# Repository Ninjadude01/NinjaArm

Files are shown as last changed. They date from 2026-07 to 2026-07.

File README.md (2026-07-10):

## NinjaArm
NinjaArm is a custom robotic arm with 3 degrees of freedom + a claw. It uses an Arduino Uno along with a servo board, 3 servos, 1 micro servo, and 4 potentiometers to control rotation. It includes a small stand for the potentiometers, and a larger display stand to hold the servo board and Arduino. I decided to create a robotic arm beacuse after building a working keyboard in real life I wanted a larger and more ambitious project. I thought that robotic arms seemed cool, so I decided to create my own from scratch. 

## Renders
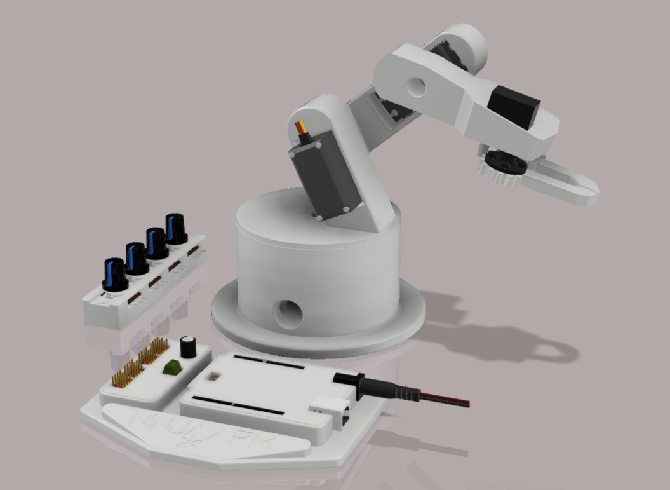
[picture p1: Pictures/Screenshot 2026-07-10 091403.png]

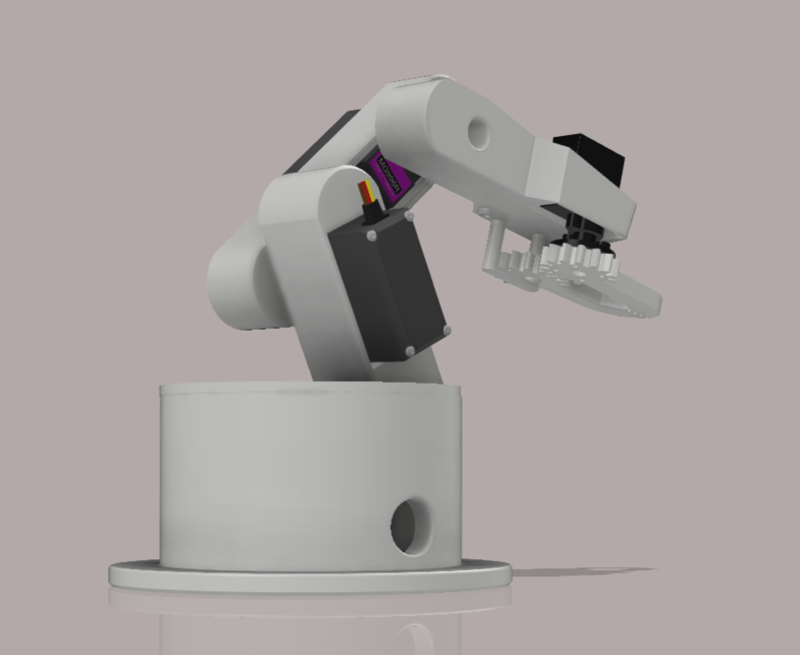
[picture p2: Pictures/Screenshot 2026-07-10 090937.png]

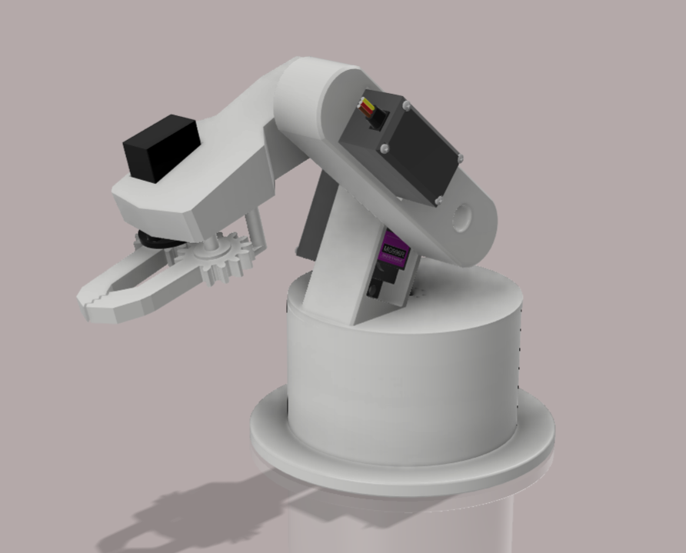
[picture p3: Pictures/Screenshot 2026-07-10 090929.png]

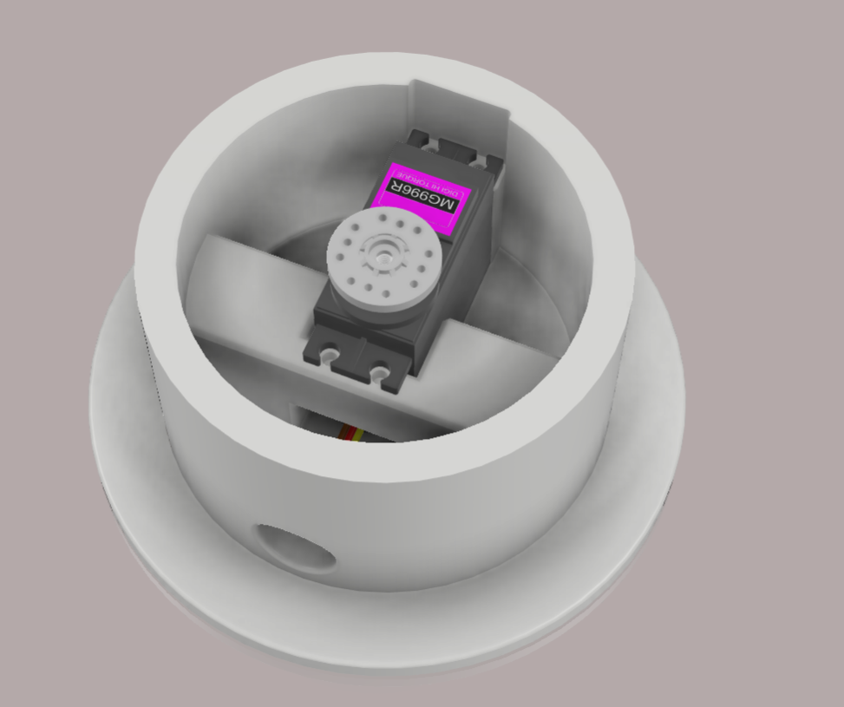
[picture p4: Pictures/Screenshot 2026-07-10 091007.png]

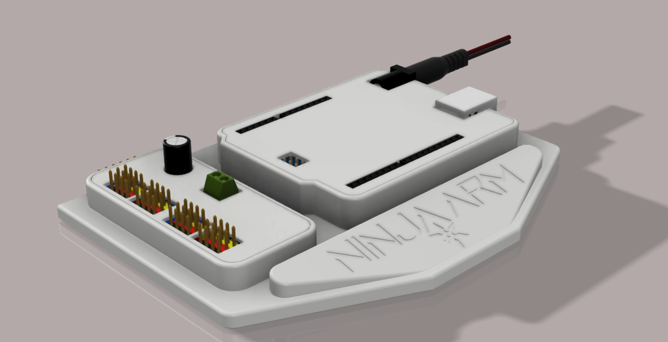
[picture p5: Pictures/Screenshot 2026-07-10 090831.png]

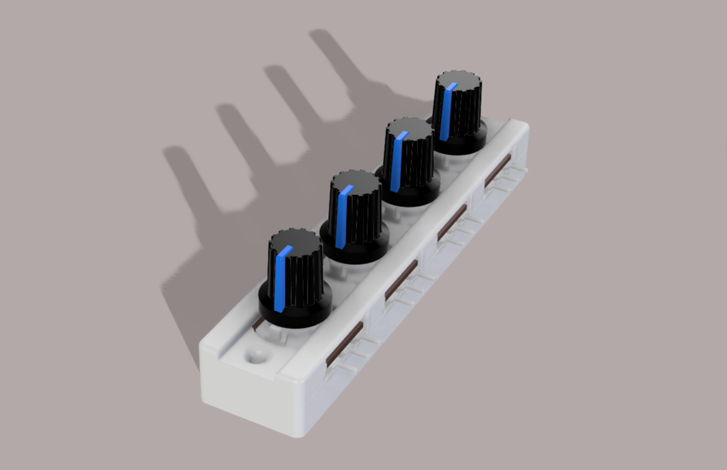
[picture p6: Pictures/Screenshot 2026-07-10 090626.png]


## Schematic Diagram
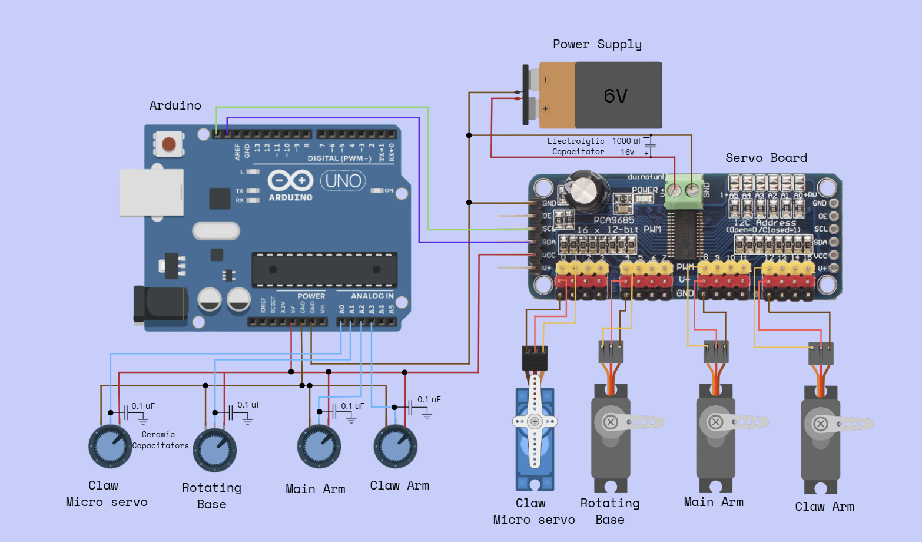
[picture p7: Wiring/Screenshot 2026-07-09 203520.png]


## Steps to Reproduce
1. Purchase all materials listed in the BOM, and print all needed parts from the CAD folder.
2. Align the heatset inserts in the correct locations and use a soldering iron set to 200℃ to slowly push them into place.
3. Place the 4 potentiometers into the knob case, put the lid ontop, and screw it into place. You can now place the knob covers ontop.
4. Place the arduino and servo board onto their respective spots on the display stand, and cover them with the lids.
5. Insert a servo into the base, main arm, and claw arm, and use the 6mm m2 screw to secure them. Insert the micro servo into the claw arm and screw that in as well.
6. Connect the micro servo horn to a claw using screws, align the second claw in the correct location, and quickly place the claw connector beneath it (screw this in as well).
7. Grab a servo horns and use 4 metal self tapping screws to secure it to its corresponding robo arm part. Repeat this two more times.
8. Use the servo horn screws to connect all three horns to their servos.
9. Follow the wiring diagram and connect all wires to the correct spots.
10. Download the .ino file found in the firmware folder, and flash it onto your arduino.
11. Use the potentiometers to control the arms, and enjoy playing with your very own NinjaArm!

Note: AI was used to assist with the firmware of this project.
## BOM
|Item|Part Name |Quantity|Description |Cost (USD)|Link |
|----|---|---|---|---|---|
|1 |Arduino Uno |1 |Microcontroller |$6.82 |https://www.aliexpress.com/item/1005012021584902.html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 |
|2 |Servo Motors |3 |MG996R (metal 180) |$13.47 |https://www.aliexpress.com/item/1005006525247038.html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 |
|3 |Smaller Servo |1 |MG90S (metal 180) |$4.42 |https://www.aliexpress.com/item/1005008626768357.html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 |
|4 |Servo Driver Board |1 | PCA9685 |$3.77 |https://www.aliexpress.com/item/1005008717177681.html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 |
|5 |Heatset Inserts |100 |M2 |$3.55 |https://www.aliexpress.com/item/1005006838108683.html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 |
|6 |Screws |50 |M2, 6mm |$1.69 |https://www.aliexpress.com/item/32973784147.html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 |
|7 |Electrolytic Capacitators|10 |1000 uF, 16v |$1.28 |https://www.aliexpress.com/item/1005005557021801.html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 |
|8 |Ceramic Capacitators |10 |0.1 uF |$3.88 |https://www.aliexpress.com/item/1005007851933584.html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 |
|9 |Stranded wire |1 |20 AWG (5m, black +red) |$7.57 |https://www.aliexpress.com/item/1005006250522147.html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|
|10  |Stranded wire |1 |22 AWG (5m, 5pc multicolor)|$15.39 |https://www.aliexpress.com/item/1005006350734418.html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 |
|11  |Potentiometers |4 |To control rotation (B10k) |$6.52 |https://www.aliexpress.com/item/1005010063122061.html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 |
|12  |Pot Knob Cap |30 |For protection |$2.99 |https://www.aliexpress.com/item/1005008733564858.html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 |
|13  |Rubber bumpers |10 |For tip of robot arm |$3.78 |https://www.aliexpress.com/item/1005003881918836.html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 |
|14  |6v power supply |1 |10A |$27.33 |https://www.aliexpress.com/item/1005008119363339.html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 |
| | | | | | |
| | | |Total |$102.46 |

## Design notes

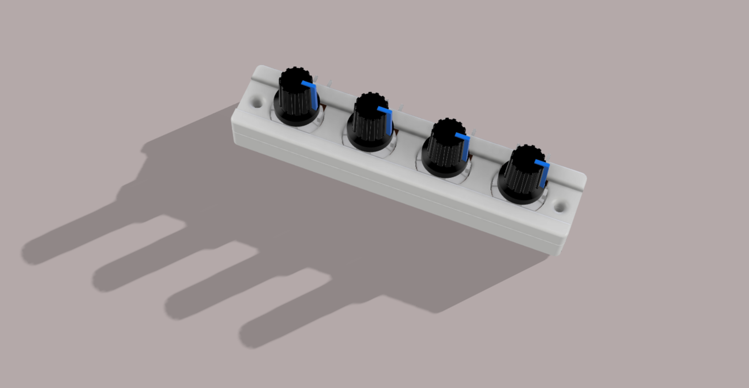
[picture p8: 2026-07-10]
Pictures/Screenshot 2026-07-10 090645.png

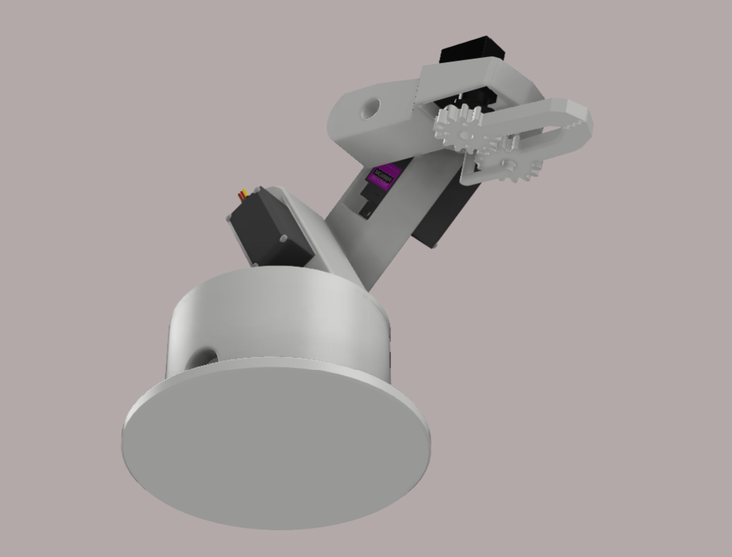
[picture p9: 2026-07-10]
Pictures/Screenshot 2026-07-10 090954.png

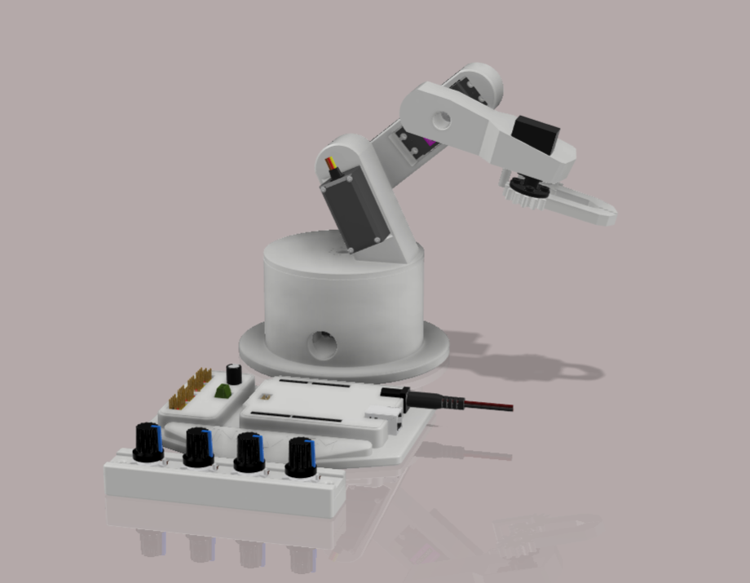
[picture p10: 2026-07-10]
Pictures/Screenshot 2026-07-10 091027.png

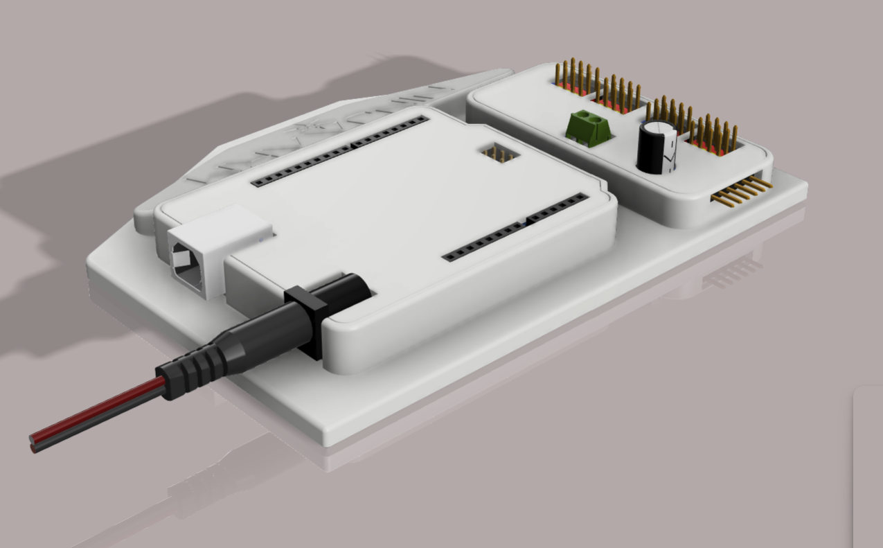
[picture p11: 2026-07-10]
Pictures/Screenshot 2026-07-10 090838.png

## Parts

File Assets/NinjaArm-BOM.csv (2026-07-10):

Item | Part Name | Quantity | Description | Cost (USD) | Link
1 | Arduino Uno | 1 | Microcontroller | $6.82 | https://www.aliexpress.com/item/1005012021584902.html?curPageLogUid=nl1zu1W5NWxa
2 | Servo Motors | 3 | MG996R (metal 180) | $13.47 | https://www.aliexpress.com/item/1005006525247038.html?mp=1
3 | Smaller Servo | 1 | MG90S (metal 180) | $4.42 | https://www.aliexpress.com/item/1005008626768357.html?mp=1
4 | Servo Driver Board | 1 | PCA9685 | $3.77 | https://www.aliexpress.com/item/1005008717177681.html?curPageLogUid=hQarf3Dfmsxr
5 | Heatset Inserts | 100 | M2 | $3.55 | https://www.aliexpress.com/item/1005006838108683.html?mp=1
6 | Screws | 50 | M2, 6mm | $1.69 | https://www.aliexpress.com/item/32973784147.html?mp=1
7 | Electrolytic Capacitators | 10 | 1000 uF, 16v | $1.28 | https://www.aliexpress.com/item/1005005557021801.html?curPageLogUid=4GRgiLxo8gIg
8 | Ceramic Capacitators | 10 | 0.1 uF | $3.88 | https://www.aliexpress.com/item/1005007851933584.html?curPageLogUid=3pynuA3Hzad2
9 | Stranded wire | 1 | 20 AWG (5m, black +red) | $7.57 | https://www.aliexpress.com/item/1005006250522147.html?curPageLogUid=9vo7UWaH5KD7
10 | Stranded wire | 1 | 22 AWG (5m, 5pc multicolor) | $15.39 | https://www.aliexpress.com/item/1005006350734418.html?curPageLogUid=8tPYifazeFcG
11 | Potentiometers | 4 | To control rotation (B10k) | $6.52 | https://www.aliexpress.com/item/1005010063122061.html?mp=1
12 | Pot Knob Cap | 30 | For protection | $2.99 | https://www.aliexpress.com/item/1005008733564858.html?curPageLogUid=KjNbnIj9rQPu
13 | Rubber bumpers | 10 | For tip of robot arm | $3.78 | https://www.aliexpress.com/item/1005003881918836.html?pdp
14 | 6v power supply | 1 | 10A | $27.33 | https://www.aliexpress.com/item/1005008119363339.html?curPageLogUid=1IkAPraOymdH
 |  |  | Total | $102.46

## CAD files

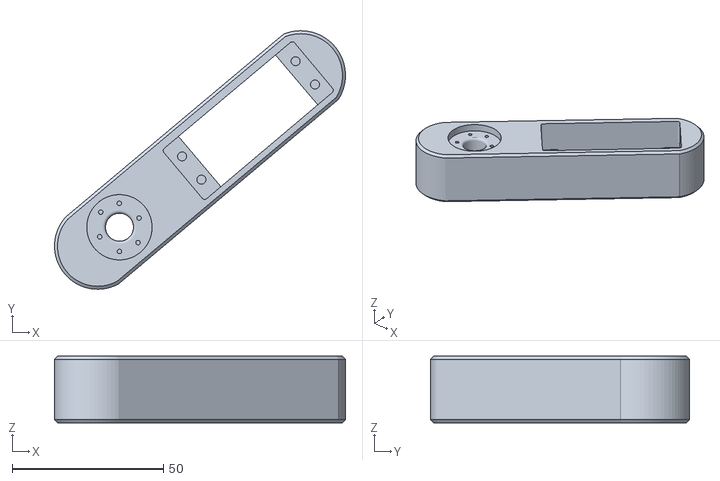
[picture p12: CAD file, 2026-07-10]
CAD/NinjaArm Main Arm.stl
96.2 x 85.5 x 22.0

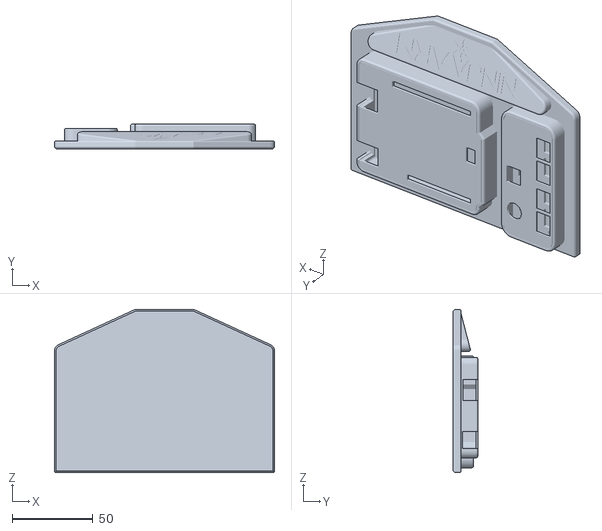
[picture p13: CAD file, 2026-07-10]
CAD/Display Stand.stl
136.0 x 15.3 x 101.0

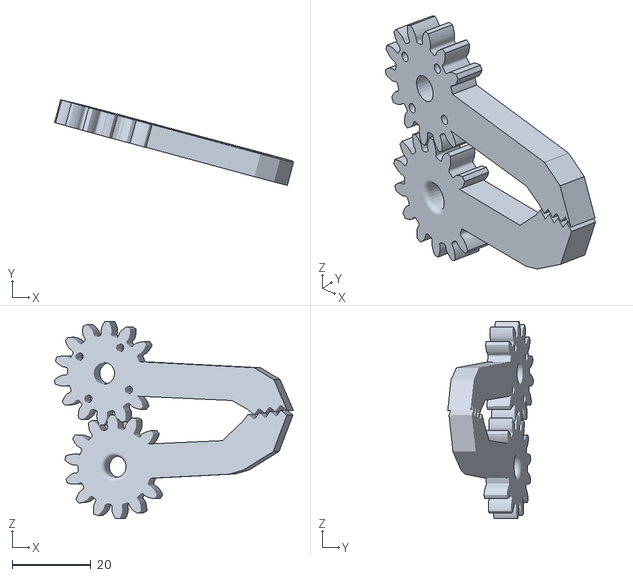
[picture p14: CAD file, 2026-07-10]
CAD/Claws with Gears.stl
60.9 x 21.8 x 50.2

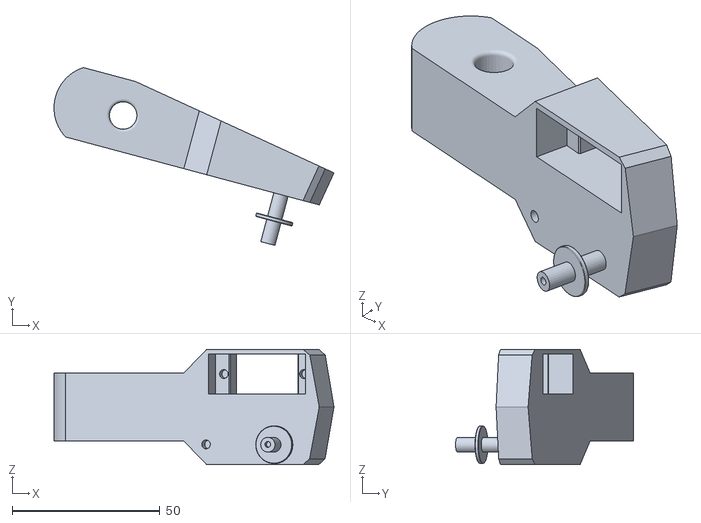
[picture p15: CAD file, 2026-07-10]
CAD/NinjaArm Claw Arm.stl
94.6 x 60.1 x 39.0

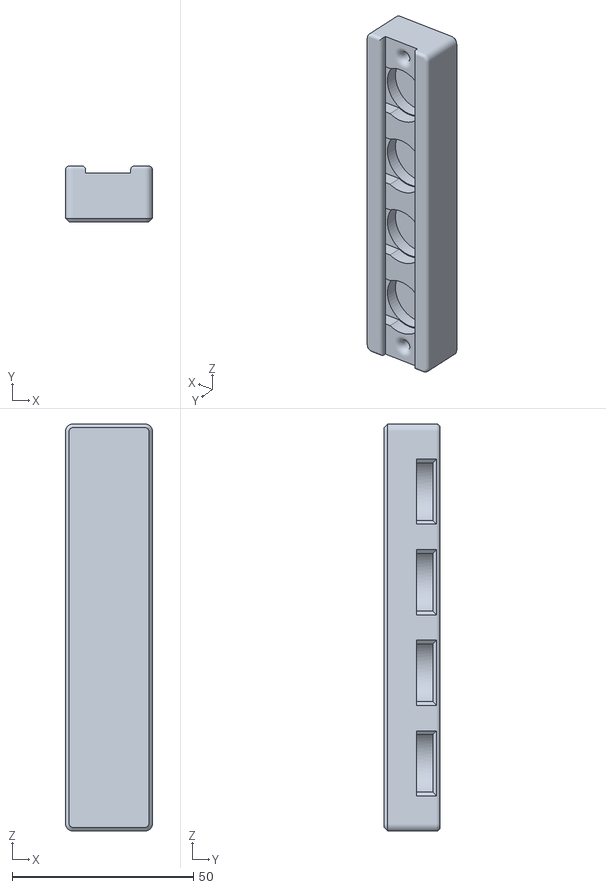
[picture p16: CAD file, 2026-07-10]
CAD/Knob Case.stl
24.0 x 15.5 x 112.4

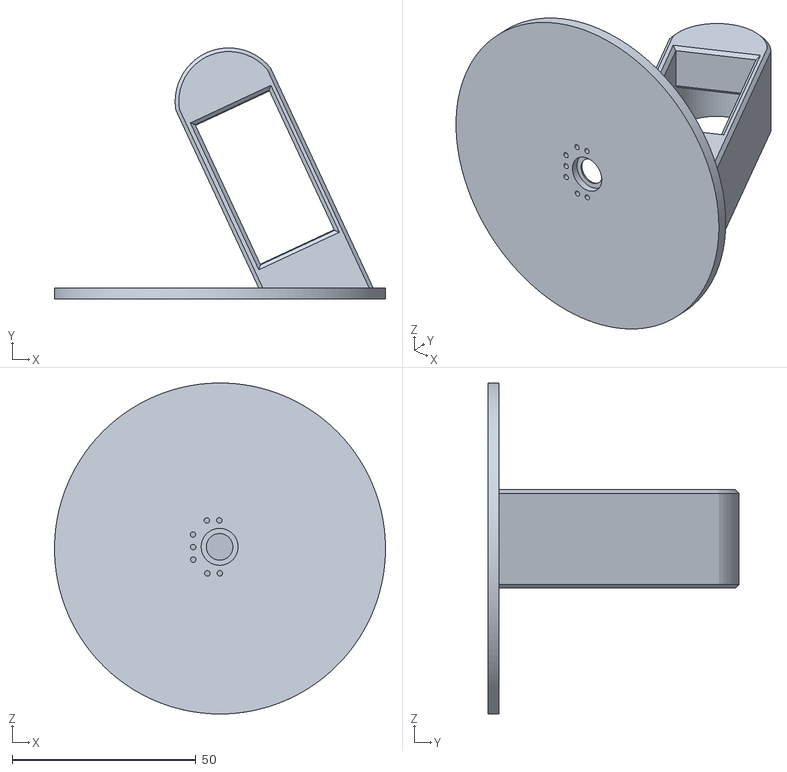
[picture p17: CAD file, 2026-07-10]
CAD/NinjaArm Rotating Platform.stl
90.0 x 68.3 x 90.0

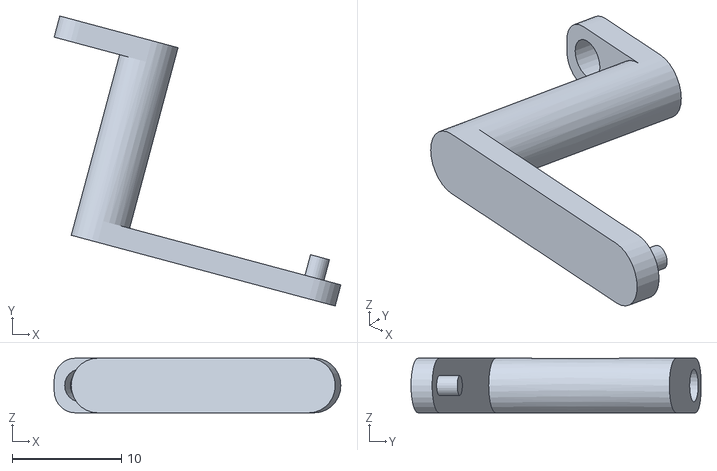
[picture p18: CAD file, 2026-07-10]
CAD/Claw Connector.stl
26.2 x 26.5 x 5.00

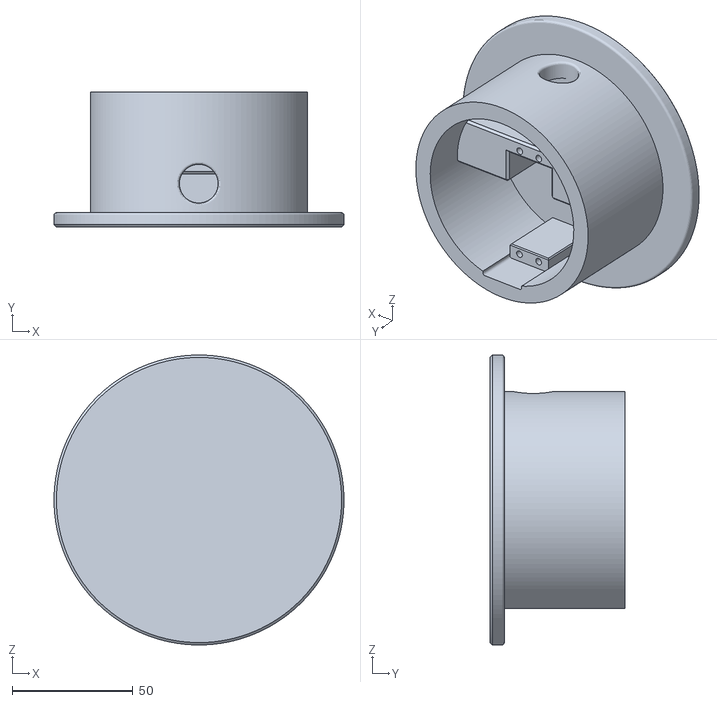
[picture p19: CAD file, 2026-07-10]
CAD/NinjaArm Base.stl
120.0 x 56.0 x 120.0

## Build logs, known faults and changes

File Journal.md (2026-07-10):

# NinjaArm — Journal 

## Entry 1
- ID: 2123
- Author: Jason
- Created At: 2026-04-14T01:08:02Z

### Content

In this session, I mainly did reseach (google searching + sourcing parts on aliexpress). I began by creating a github repository and adding in some basic folders and header names, then moved to creating a word document containing everything related to my project. I did lots of  reseach on what materials to choose for the Arm, and then wrote it down in the document. Finally, I created a spreadsheet and started working on my BOM. I will be using aliexpress to source most of my parts, as it is cheaper to buy from there compared to amazon. 



### Recording Links

- https://public.lapse-hackclub.link/timelapses/IpcSVlLANcHv/timelapse-IpcSVlLANcHv.mp4
- https://public.lapse-hackclub.link/timelapses/4vyFI6BsOFDF/timelapse-4vyFI6BsOFDF.mp4
- https://public.lapse-hackclub.link/timelapses/DUxu6G1-t0e3/timelapse-DUxu6G1-t0e3.mp4

## Entry 2
- ID: 2265
- Author: Jason
- Created At: 2026-04-15T02:30:29Z

### Content

In this session, I got the majority of my BOM complete! I did some reseach and spent most of my time looking through aliexpress and shopping for parts. Theres still a few more changes that I want to make, but its mostly complete. Heres a general part by part explanation:

- Arduino Uno: will be the dev board I am using, it is cheap and simple to use
- 3 x MG996R servos - these will be metal, as metal is mcuh stronger and durable than the plastic servos. They will be the main arm servos
- 1 x MG90S - also metal, its a micro servo and will be used for the opening and closing of the claw
- 1 x PCA9685 - servo driver board, allows you to control the servos using 2 arduino pins
- Capacitors - 100uF caps will be placed across the power rails near the servos, a 1000 uF cap will be placed near the main power rail
- 20 AWG wire for power from psu to servo power rails
-22 AWG wire for potentiometers or extend servos if needed
-6v 10a psu: powers all 4 servos
-potentiometers: allows you to control each indiviual joint
-rubber bumpers: for the tip of the claw, allows arm to grip things



### Recording Links

- https://public.lapse-hackclub.link/timelapses/Jc7SRH6eZsX8/timelapse-Jc7SRH6eZsX8.mp4

## Entry 3
- ID: 2391
- Author: Jason
- Created At: 2026-04-16T00:56:05Z

### Content

In this session, I seached on the internet for step files for parts of my project. Grabcad was very useful, as I found most of the files needed there, without much trouble. I then imported the step files of an arduino uno, various types of screws (to attach servos to their horns), an MG90s + MG996R, a potentiometer, and a PCA9685 servo driver board. Then, after laying out all the items, I carefully placed the horns into the servos, using section analysis (a tool that allows you to essentially see through layers of an object, so you can see how everything looks inside, kinda like an x-ray) to make sure the horn was properly aligned, and after I inserted the correct screw for that motor.



### Recording Links

- https://public.lapse-hackclub.link/timelapses/hgGNnR2oPSYi/timelapse-hgGNnR2oPSYi.mp4

## Entry 4
- ID: 2393
- Author: Jason
- Created At: 2026-04-16T01:03:42Z

### Content

In this session, I began working on a small stand which will hold the arduino and the servo board. I first did some searching to see where other robotic arms had placed their microcontroler and servo board, and noticed that a few had small stands for them, which made me want to make my own. I created a skech on the xy plane, and made simple outlines for the 2 objects. Then, I began working on the outlines in more detail, such as rounding the edges and making small indents for the underside of the boards (as they both have pins sticking out from benath, and if I just created a flat surface those pins would get damaged). Finally, I added circles in the designated areas, which will later become mounting holes (I will place screws in those areas to secure the boards and make sure they dont come off).





### Recording Links

- https://public.lapse-hackclub.link/timelapses/eF8MB6bZOIM5/timelapse-eF8MB6bZOIM5.mp4
- https://public.lapse-hackclub.link/timelapses/rdZA9uExyc7x/timelapse-rdZA9uExyc7x.mp4

## Entry 5
- ID: 2524
- Author: Jason
- Created At: 2026-04-17T02:44:50Z

### Content

In this session, I worked on the stand for the servo drive board. I started off by trying to re-design the platform, as I thought that there was a simpler way to do it, which was just to make a few tall and wide support pillars, with heatset inserts placed inside the beams. However, this idea turned out to not be a viable option, as the thick support pillars collided with the pins sticking out from the bottom of the servo board. So, I decided to undo what I just did and go back to its original state before I modified it. However, after adjusting the size of the holes for pins to rest on, I had trouble extruding those holes, so I tried to change the sketch plane height. This did not go well, as there was now a green border to the sketched items (which did not seem good), so I deleted the old base and started over again. I quickly got back to where I left off, and from there I made the outline of the walls surrounding the board, as well as a cover. I plan to later add a snap-fit mechanism to the lid, as right now it is freely sitting on top of the walls.





### Recording Links

- https://public.lapse-hackclub.link/timelapses/2_e7yR5VGdhH/timelapse-2_e7yR5VGdhH.mp4
- https://public.lapse-hackclub.link/timelapses/Km80DT9tvseS/timelapse-Km80DT9tvseS.mp4

## Entry 6
- ID: 2664
- Author: Jason
- Created At: 2026-04-18T03:19:59Z

### Content

In this session, I finished up the arduino + servo board display stand. I started by creating a "shell" of the servo case, which would keep the lid in place. 



Next, I designed the case for the arduino board. I had some trouble here, as I had moved the position of the arduino but whenever I opened up my old sketch it still had the old position saved. After some searching, I decided to just give up, as it would be much easier to copy the old outline and paste it into a new sketch (with the updated location of the arduino). I made indents into the main rectangle base for pins on the underside of the ardino, and createdlid with not much difficulty. I did struggle a bit when trying to create a "shell," as the bodys kept merging and breaking. 

(picture of arduino case w/o lid)



I made the lids of both items slightly smaller than the shell, as you have to account for 3d printing toleraces and how easily it will be able to fit. I decided to make it 0.2mm smaller, as I wanted it to fit very snugly. 

Additionally, I spent some time renaming and organizing the bodys, as eventualy I will have much more and being organized will be a basic requirement. I also chamfered the bottom (to make it easier to print), and filleted the top edges to make it look nicer. 

Finally, I started designing the base for my robot arm. I started with a cylindrical shape (as it looks better than a square), and managed to create basic supports that the motor will screw into to secure itself. I addes 4 small feet around the outer ring to further help secure the base, as without strong support the arm could topple over. 




### Recording Links

- https://public.lapse-hackclub.link/timelapses/geJ_BHuLp1tK/timelapse-geJ_BHuLp1tK.mp4
- https://public.lapse-hackclub.link/timelapses/hTSPiJ4HO5i3/timelapse-hTSPiJ4HO5i3.mp4
- https://public.lapse-hackclub.link/timelapses/mdy9kUz6RKbB/timelapse-mdy9kUz6RKbB.mp4

## Entry 7
- ID: 2817
- Author: Jason
- Created At: 2026-04-19T03:26:01Z

### Content

In this session, I organized all of the files for my project inside of fusion. This is because there were lots of files in my robot arm folder (such as screws, servos, and ardinos), which is why I decided to make 3 sub-folders to help keep everything organized. Then, I made copies of my main design because I had a bunch of small cad items in one design, and I did not want everything to be cluttered and together. Next, I worked on the support structure for the servo controlling the rotation of my base, I added holes for heatset inserts (so I could screw the servos down). This is when I realized that the rotating part of the servo was supposed to be in the exact centre of the cylindrical base, as if it wasnn't it would rotate very weirdly. I then spent the rest of the session trying to centre the servo and re-arrange the supports to match the new location of the servo. I had some difficulty doing so, for example the sketches kept showing old positioning, but in the end I managed to centre it and adjust the supports to match. 





### Recording Links

- https://public.lapse-hackclub.link/timelapses/Nibm82Z2SXC8/timelapse-Nibm82Z2SXC8.mp4
- https://public.lapse-hackclub.link/timelapses/VLnR4CDz4hCW/timelapse-VLnR4CDz4hCW.mp4

## Entry 8
- ID: 2991
- Author: Jason
- Created At: 2026-04-20T01:00:56Z

### Content

In this session, I removed the supporting legs for my robotic arm base. This is because I did not like the look of them, and I plan to replace them with a simple larger circular ring (which I plan to do in a later session.) I also realized that one pair of mounting tabs were cutting into the side of the inner cylinder. To solve this, I created a small pocket of space for the mounting tab to reside in, solving the problem. 



Another thing I realized this session was that I would also have to plan for other cables to pass through the base and exit though a small openeing. This changed everything, as my old design only accounted for one cable coming from one direction, meaning that I had to redesign half of the inner section to accomodate for additional cables. I did this by creating a horizontal "bridge" on either sides of the cable-facing mounting tab, which resulted in much more open space for other cables to pass through. Finally, I added circle-shaped cuts to the "bridge," which would allow me to put heatset inserts in, providing a place for me to screw down the servo motor securely. 





### Recording Links

- https://public.lapse-hackclub.link/timelapses/We8E2fnWdrky/timelapse-We8E2fnWdrky.mp4
- https://public.lapse-hackclub.link/timelapses/lg5yFUJsfQNC/timelapse-lg5yFUJsfQNC.mp4

## Entry 9
- ID: 3137
- Author: Jason
- Created At: 2026-04-21T02:08:18Z

### Content

In this session, I created a small circular ring around my base to serve as supports. I chose to do a ring instead of regular feet sticking out as I thought it looked more aesteically pleasing. Then, I renamed some sketches and analysises to organize them (as I have a lot, and I will soon have much more, so keeping them organized is important), and extruded a hole for cables to exit the cylinder base. Next, I created a new component for my project, which was the rotating platform! I created some small holes on the platform, providing a way to securely connect it to the servo horn down below. I spent a very long time doing this, as I couln't decide what order or shape I wanted to arrange my screws in. I eventually decided on a rectangular shpae with 4 holes, as it was simple yet sturdy. I then created a sketch on the rotating platform, and extruded an H shaped pillar, as I planned on attaching my second servo it it verticaly. This is when I realized that it did not look cool, so I decided to take inspiration from other robotic arm designs, and decided to have an angulared support beam. I spent the rest of the session working on this angular beam, and I had some struggles doing so. This is because it was hard for me to get an exact outline of the servo when trying to create a rectangle that would cut into the arm, but I eventualy got a rough outline in the end. 

Screenshot 2026-04-20 220411.png



### Recording Links

- https://public.lapse-hackclub.link/timelapses/5guBlroU3n_b/timelapse-5guBlroU3n_b.mp4
- https://public.lapse-hackclub.link/timelapses/4ReAiGAaDVnr/timelapse-4ReAiGAaDVnr.mp4

## Entry 10
- ID: 3303
- Author: Jason
- Created At: 2026-04-22T00:22:11Z

### Content

In this session, I learned how to properly use components. This is because before, I did not understand what activiating a component meant or did, but after doing some reseach I now know, and I properly activated my spinning platform component and created bodies and sketches inside of there. Next, I decided to redo my base arm as I did not like the way it looked or was designed. I started by recreating the stand vertically (as it is much easier to do it this way compared to starting off on an angle), and made outlines around the MG996R motor. I then extruded those outlines and placed it onto the platform on an angle. I also redid the circular top of the platform arm, made the base cylinder smaller (as I thought it looked too big and would still be stable with less filament), and chamfered the edges of the arm for aestetics. I also figured out how I accualy wanted to connect each limb to another, as previously I did not really understand how it worked, but now I do (I now realize that the servo horn has to be sticking out on the other side in order to connect to the limb. I also left the back side of the servo open, as designing the arm to cover it entirely would be too bulky and inefficient. Instead, I will later create a small plastic cover to cover that backside.





### Recording Links

- https://public.lapse-hackclub.link/timelapses/TwBLrp8ooQ4N/timelapse-TwBLrp8ooQ4N.mp4
- https://public.lapse-hackclub.link/timelapses/fhSWxYo0m7e6/timelapse-fhSWxYo0m7e6.mp4

## Entry 11
- ID: 3486
- Author: Jason
- Created At: 2026-04-23T02:01:48Z

### Content

In this session, I improved the cad design of my display stand, which currently holds my servo board as well as my microcontroller. I started by reversing the direction of my servo board case, as it made sense for the horizontal pins sticking out to point away from me. The reason I wanted to reverse that case specificaly and not just the entire design was because I still wanted my arduino to point to the right side, as I planned on having my laptop connect to it from the right. I also added a cool diagonal slant at the front of the display, with the name of my project, NinjaArm, engraved onto it, as well as a cool shuriken. However, when trying to engrave the text, I struggled for a long time, as it said "error, can't extrude." I was very confused when this message popped up, but I thought maybe it was because I was trying to extrude on a slant. After doing some reaseach and debugging to no avail, I stumbled across a source that mentioned something about the font possibly being the issue. I then went back into fusion and realized that I had selected a custom font I downloaded a while ago, which must have been the reason it wasent working as it was not a native fusion text font. Since I still wanted to use the same font, I decided to just make outlines of every letter and cut it into the stand that way, which is what I slowly did. Eventually, it did work so I am glad about that. 





### Recording Links

- https://public.lapse-hackclub.link/timelapses/nIEcjLKMZyUB/timelapse-nIEcjLKMZyUB.mp4
- https://public.lapse-hackclub.link/timelapses/Yc4cUZNG80R1/timelapse-Yc4cUZNG80R1.mp4

## Entry 12
- ID: 3969
- Author: Jason
- Created At: 2026-04-26T01:45:20Z

### Content

In this session, I continued to work on the arm attached to the rotating base platform, and started the secondary arm. I first resized the shuriken on my display stand as it was too large, then imported that file into my main robo arm project so I could see it next to my robotic arm base. Next,  I redid the circle cutout for the servo horn, as when looking at it through section analysis, it was slightly misaligned. I fixed this by projecting the outline of the servo onto my spinning platform, then offsetting that outline by a few mm to leave some wiggle room, and finnaly extruding that outline into the platform to make a small cut. I then decided to make my platform arm 1mm thicker on each side, as I did not think 2mm on each side was strong enough to support the robotic arm. This meant that I had to redo the semicircle at the top of the arm (as I couldn't figure out how to make the circle line up with the walls in the sketch), but after some time I managed to do it. Next, I created a new component for my second arm peice, and I started off by wanting a semi-circle on each side, but then I realized that it would be tricky if I wanted to extend the length of the arm, so I ended up starting with only a semi circle on the bottom (near the point of rotation). After doing some more work on the second arm, I realized that I had forgoten to include mounting screw cutouts for my other project of a 65% keyboard, as there were none when I opened up the cad file. However, after downloading the step file I had previously uploaded to my github repository, it seemed like I did before, but the changes wern't saved, which was very strange. 





### Recording Links

- https://public.lapse-hackclub.link/timelapses/tMvJm5J4AH0z/timelapse-tMvJm5J4AH0z.mp4
- https://public.lapse-hackclub.link/timelapses/OSH5WVhMfeAZ/timelapse-OSH5WVhMfeAZ.mp4

## Entry 13
- ID: 4425
- Author: Jason
- Created At: 2026-04-29T01:11:18Z

### Content

In this session, I worked on the second arm part for my robotic arm. I started by adujusting the screw holes on the spinning platform that are used to connect it to the servo horn below, as they were all slighly misalgined. Then, I tried spliting my platform to break it down into two smaller sections, as it would make it easier to edit in the future. However, after doing some searching and trying for a while, I did not figure out how to do it so I gave up. Next, I began working on the second arm, and added screw holes to it. I also reduced the thickness of the side of the arm facing the rotating part, as after doing some thinking I realized that it would be very hard to screw screws onto it, and leaving some more space inbetween the moving parts would be a good idea. Finally, I added a section at the end of the arm to mount my third servo motor, as well as mounting holes for that. 




### Recording Links

- https://public.lapse-hackclub.link/timelapses/ca2c3Rs_o2GI/timelapse-ca2c3Rs_o2GI.mp4
- https://public.lapse-hackclub.link/timelapses/LdSGJ1KoMtYP/timelapse-LdSGJ1KoMtYP.mp4

## Entry 14
- ID: 4578
- Author: Jason
- Created At: 2026-04-30T03:58:52Z

### Content

In this session, I worked on creating the final moving peice for my robotic arm. I started by learning how to rotate a component from a certian point, and did so by seraching online. Next, I rounded off the second arm and chamfered it to make it look better, and copied it to use as the general structure of my third arm. However, I realized that if I made a modification to the copied arm, the same change would occur on the original arm, which is not what I wanted. I solved this by first copying the arm, but clicking "paste new," which would paste it as a seperate item. Finally, I arranged the last servo motor in the correct position as a claw, but I then realized that I had initialy intened to use a smaller servo motor specifically for the claw. So, tried importing the motor with screws and the horn into my fusion project, however I tried many times and it could not work. After doing lots of searching and testing to no avail, I decided to just remove everything else from the file the small servo was in, allowing me to easily copy and paste that servo into the main project. 





### Recording Links

- https://public.lapse-hackclub.link/timelapses/T2GELSiv76n6/timelapse-T2GELSiv76n6.mp4
- https://public.lapse-hackclub.link/timelapses/NU4N_BhAsdEZ/timelapse-NU4N_BhAsdEZ.mp4

## Entry 15
- ID: 4715
- Author: Jason
- Created At: 2026-05-01T03:58:57Z

### Content

In this session, I began working on the claw component of the robotic arm, and I think that it has become one of my favorite parts to design! I started by first setting up the mini servo in the general area on the arm where I wanted it to be in, and did some thinking on how I wanted the claw mechanism to work. I originally had the spinning part of the servo placed in the exact centre, but I realized it would make sense to place it slightly off centred, as I wanted my mechanism to use two gears to work. 

This is a picture of how I intend my claw to look like, as you can see, one servo turns one gear, which turns another gear, with both gears being connected to the claw mini arm. I followed a simple tutorial to help me model the parts needed for my claw, as I had no idea how to begin, or how I would model the tooth spaces on the gears. I managed to get 3 parts done, which isnt too much but its better than nothing. 


### Recording Links

- https://public.lapse-hackclub.link/timelapses/jWlC54azbOX8/timelapse-jWlC54azbOX8.mp4

## Entry 16
- ID: 4857
- Author: Jason
- Created At: 2026-05-02T03:58:49Z

### Content

In this session, I decided to scrap my original idea of following a tutorial for a claw. I decided to restart and design my own from scratch, as I thought it would be more fun and unique. I started by creating a skech on the mini servo's horn, and created a similar claw-shape as I did before. However, this time my idea was to connect a rotating gear directly to the claw, without any extra long supports to help. This means that it will be much easier for me to design. Next, I did reseach on how to add a gear into fusion, and I found a tutorial and quickly figured out how. I spent some time creating multiple gears, as the gear created was slightly different from how I wanted it to be, for example sometimes they were too large or had too many gear teeth. After creating the perfect gear, I merged it with my pre-made arm, and duplicated it. There is currently two green circles floating way above my gears, I think those are the rotation points but I dont know why they are so high up. 






### Recording Links

- https://public.lapse-hackclub.link/timelapses/Cqg6LuCNXkWv/timelapse-Cqg6LuCNXkWv.mp4
- https://public.lapse-hackclub.link/timelapses/hUtEEVAKPwsk/timelapse-hUtEEVAKPwsk.mp4

## Entry 17
- ID: 5215
- Author: Jason
- Created At: 2026-05-03T03:57:20Z

### Content

In this session, I continued to work on the design of the claw gripper piece for my robotic arm. I started by transfering my claw design over to the main project file and creating a rectangular opening on the arm so I would be able to mount the servo and hold it in place. I added two holes in the arm to fit m2 heatset inserts, and tried deleting the old mounting holes on the claw as they didnt match up with the servo horn orientation in the main file. I fixed this my going back into the file containing the claw arm design, orienting the claw the same way as it was in the main file, and updating the main file with the new changes. Now that I think about it, I could have solved this problem by simpily rotating the horn and claw in the main file.... I also rotated the entire arm to make it look better, and also improved the design by adding unique cut angles and chamfers/fillets. I still need to figure out a way to attach the second claw part to the arm, however I plan on doing that in the next session. 




### Recording Links

- https://public.lapse-hackclub.link/timelapses/IzSoLVsRZi1q/timelapse-IzSoLVsRZi1q.mp4
- https://public.lapse-hackclub.link/timelapses/7HTEs1N0EzwE/timelapse-7HTEs1N0EzwE.mp4

## Entry 18
- ID: 6515
- Author: Jason
- Created At: 2026-05-11T00:20:59Z

### Content

In this session, I made lots of small design improvements. To start, I redid and improved the small cut at my base, which was made because one of the mounting tabs of a servo was colliding with the inner rim of the circular base. I then looked and re-analyzed my components to ensure everything was in order, and re-oriented some parts that were incorrectly rotated. Finally, I worked on the claw section, and did some reseach on how to split a body. This is because I realized that if I added a second gripper, the claw would be off-centred, so I would have to shift the servo section slightly in order to fix this. I managed to shift it, however I am still far from being done.




### Recording Links

- https://public.lapse-hackclub.link/timelapses/j1SjTv3xPzV6/timelapse-j1SjTv3xPzV6.mp4
- https://public.lapse-hackclub.link/timelapses/tEhKdpJviBKM/timelapse-tEhKdpJviBKM.mp4

## Entry 19
- ID: 10552
- Author: Jason
- Created At: 2026-05-31T02:14:06Z

### Content

In this session, I made many small changes as well as improved the claw design. I started by checking all my dimensions, for example I checked the heatset insert holes. I found that some were a bit too large or too deep, so I easily corrected them to the correct dimesnion of a 3mm diameter, being 3mm deep. Next, I realized that there was not a possible way that I would be able to screw in most of my components, so I made lots of holes for the main screws connecting the horns into the servo. This is because I planned to screw the arms and moving platform to the servo horns before screwing them into the motor, as it would make things easier. Next, I continued to work on the claw arm mechanism. I added a second claw, however I realized that there would be nothing holding it in place. So, I made this small contraption that would allow me to place the secondary claw pincer onto a extruded cylinder, then keep it in place (while allowing it to freely rotate) with a small 3d printed part that would be screwed into the claw.





### Recording Links

- https://public.lapse-hackclub.link/timelapses/HxRsaz0jpIKl/timelapse-HxRsaz0jpIKl.mp4
- https://public.lapse-hackclub.link/timelapses/57ekqN95MkHz/timelapse-57ekqN95MkHz.mp4

## Entry 20
- ID: 10782
- Author: Jason
- Created At: 2026-05-31T23:58:00Z

### Content

In this session, I created a small stand to hold the 4 potentiometers that I will be using to control the servos. I started by finding the cad files for a potentiometer online, downloading them, and aranging 4 of them equaly spaced in a row. I created a rectangular base, as well as a small cover with holes for the rotating knob part, to secure them (ensuring they dont fall out) which is connected to the base through screws. Finally, I found the step files for the knob caps online, and added them in. 




### Recording Links

- https://public.lapse-hackclub.link/timelapses/WNaReajOqCzP/timelapse-WNaReajOqCzP.mp4
- https://public.lapse-hackclub.link/timelapses/Bku35VmY-2t7/timelapse-Bku35VmY-2t7.mp4
- https://public.lapse-hackclub.link/timelapses/s41LYirAMptS/timelapse-s41LYirAMptS.mp4

## Entry 21
- ID: 11023
- Author: Jason
- Created At: 2026-06-02T01:42:08Z

### Content

In this session, I made most of the schematic for my robotic arm project. I tried looking at many sites to do this such as tinkercad, however they all did not have the servo board that I needed to include. So, I decided to make my own schematic in canva whiteboard, and imported images of my components. I wired them together using colored lines, and was very satisfying to slowly see all of my parts connect together electrically. In my next session I have to add capacitators into my diagram, as I forgot to include those. I also almost forgot to include my potentiometers too, but I managed to remember.

Screenshot 2026-06-01 213431.png

### Recording Links

- https://public.lapse-hackclub.link/timelapses/c19503Z6Bjya/timelapse-c19503Z6Bjya.mp4
- https://public.lapse-hackclub.link/timelapses/qy5zU4mFUKlV/timelapse-qy5zU4mFUKlV.mp4

## Entry 22
- ID: 16543
- Author: Jason
- Created At: 2026-07-10T10:54:56Z

### Content

In this session, I finished up the scematic diagram of my robotic arm by adding in some capaciatators where needed. I also did some reseach and finalized my BOM, I ended up changing my 4mm m2 screws to 6mm ones, as they were too short to work well in my designs. I made the servo horn screw holes in my rotating platform and arms shorter, as they only needed to be 10mm deep (the length of the screws I had were 13mm).
Next, I went into the render section of fusion and took nice photos of my project. I made sure to use a nice looking background and different perspectives and lighting. Finally, I downloaded all of the cad files and uploaded them to the github repository, converted my csv to markdown (so I could paste it in the bom section of my readme), and wrote assembly instructions so anyone could easily repliacte my project at home.


Screenshot 2026-07-10 091403.png

### Recording Links

- https://lookout.hackclub.com/api/media/f6655046-3b48-4eee-98cb-9e46a2fe07f3/video.mp4
- https://lookout.hackclub.com/api/media/6a2de0c9-d5af-4267-b48c-3b403d785838/video.mp4
- https://lookout.hackclub.com/api/media/f62a8af8-245a-4a91-9184-998d22d92609/video.mp4

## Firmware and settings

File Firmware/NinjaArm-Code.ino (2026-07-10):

#include <Wire.h>
#include <Adafruit_PWMServoDriver.h>
Adafruit_PWMServoDriver srvBoard = Adafruit_PWMServoDriver();

const int potCLAW = A0;
const int potBASE = A1;
const int potMAIN = A2;
const int potARM  = A3;

const int chaCLAW = 0;
const int chaBASE = 4;
const int chaMAIN = 8;
const int chaARM  = 12;

#define servoMin 150 
#define servoMax 600 

void setup() {
  Serial.begin(9600);
  srvBoard.begin();
  srvBoard.setOscillatorFrequency(27000000);
  srvBoard.setPWMFreq(50);
  delay(10);
}

void loop() {
  int potClawV = analogRead(potCLAW);
  int potBaseV = analogRead(potBASE);
  int potMainV = analogRead(potMAIN);
  int potArmV  = analogRead(potARM);

  int pulseClaw = map(potClawV, 0, 1023, servoMin, servoMax);
  int pulseBase = map(potBaseV, 0, 1023, servoMin, servoMax);
  int pulseMain = map(potMainV, 0, 1023, servoMin, servoMax);
  int pulseArm  = map(potArmV,  0, 1023, servoMin, servoMax);

  srvBoard.setPWM(chaCLAW, 0, pulseClaw);
  srvBoard.setPWM(chaBASE, 0, pulseBase);
  srvBoard.setPWM(chaMAIN, 0, pulseMain);
  srvBoard.setPWM(chaARM,  0, pulseArm);

  delay(20);
}
